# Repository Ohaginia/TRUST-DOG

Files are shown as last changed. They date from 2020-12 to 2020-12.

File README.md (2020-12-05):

# TRUST-DOG PROJECT
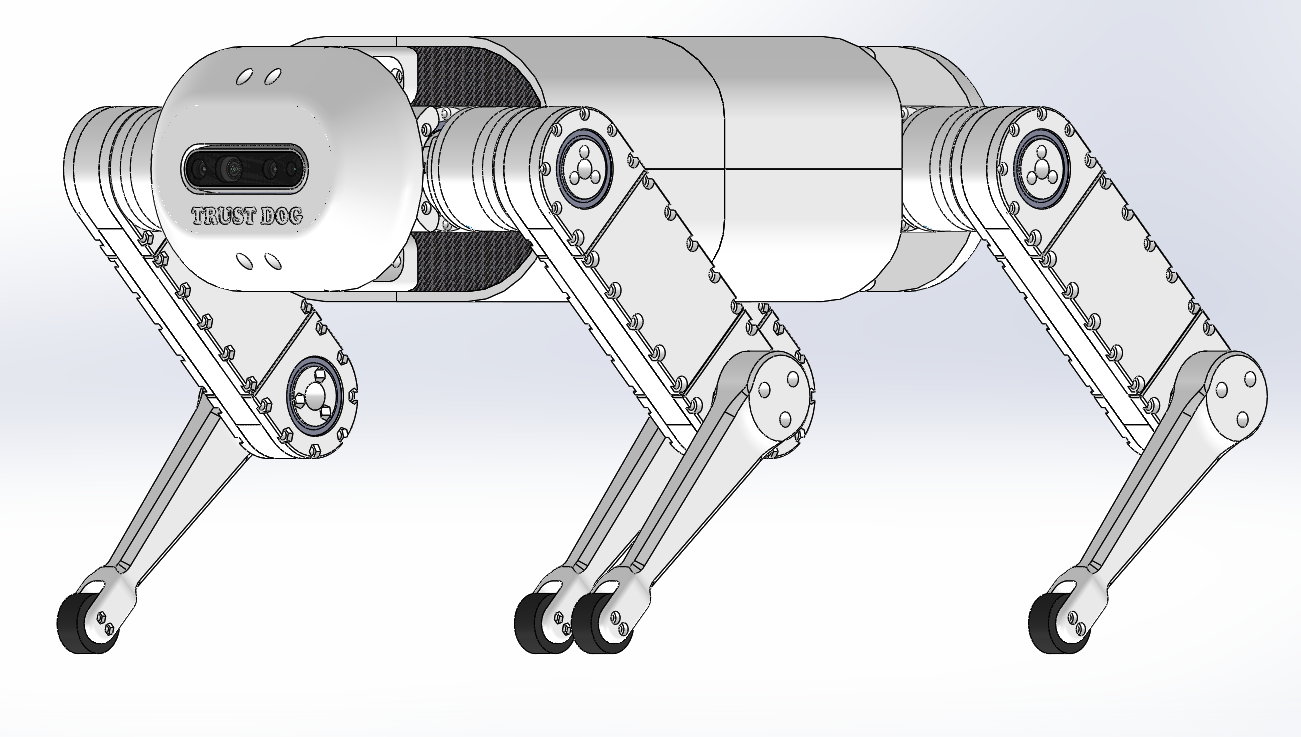
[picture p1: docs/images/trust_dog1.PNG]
trust_dog
      
 
## 0.プロジェクト概要
ドローン用ブラシレスモータを使って、Spot miniのような動的な制御ができる四足歩行ロボットを作るというプロジェクト。 
## 1.ハードウェア
### 1.1. ハードウェア概要

一脚につき3軸のアクチュエータを有する、全12軸四脚ロボット。  
構成自体はSpot miniやLaikagoと同じ。  
縦464[mm] × 横337[mm] × 高さ334[mm] (上図姿勢時）

### 1.2. アクチュエータ
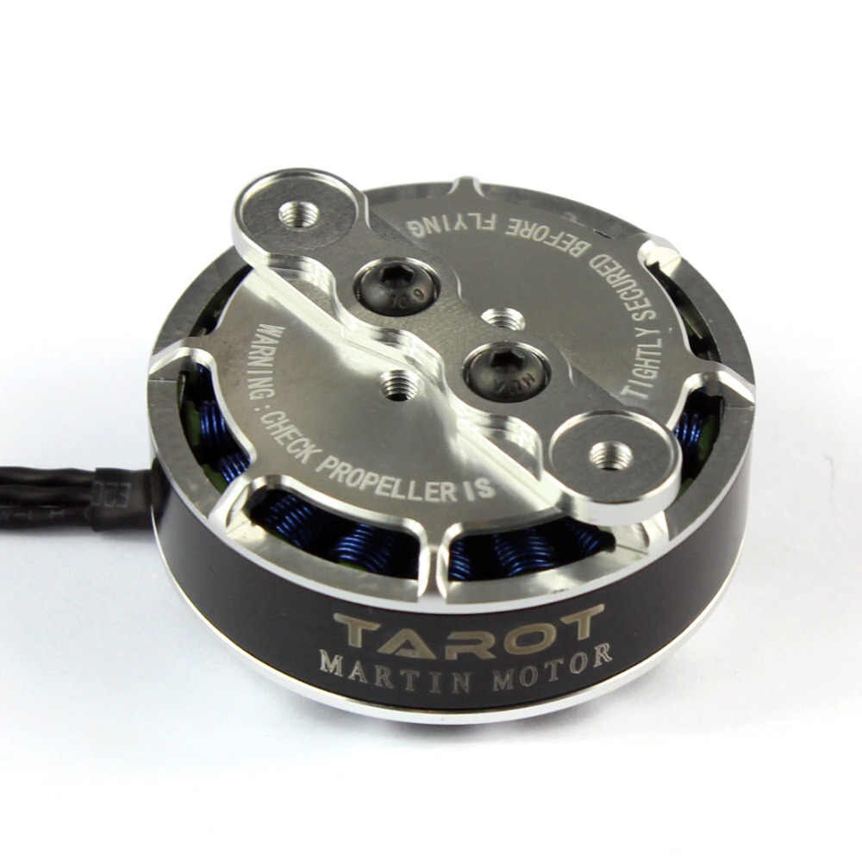
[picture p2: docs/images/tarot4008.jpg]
tarot4008
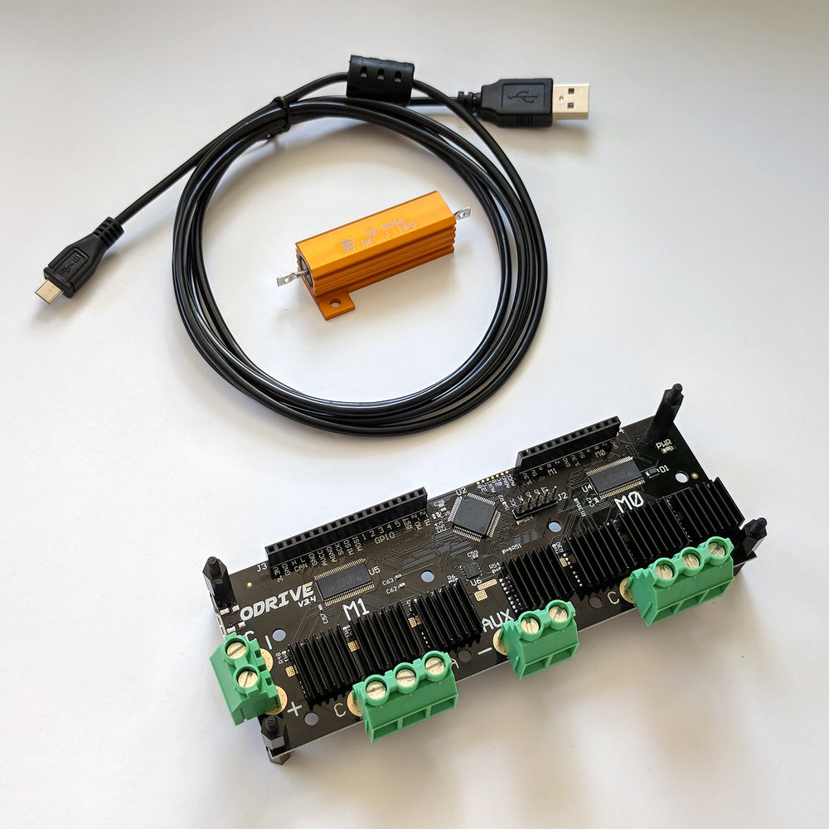
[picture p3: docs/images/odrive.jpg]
ODrive
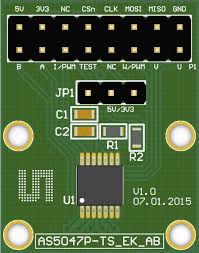
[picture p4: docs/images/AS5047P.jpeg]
AS5047P
  　    

+ モータ：[tarot4008　330kv](https://www.aliexpress.com/i/32697306634.html)
+ ドライバ：[Odrive v3.6](https://odriverobotics.com/)  
+ エンコーダ：[AS5047P](https://www.mouser.jp/ProductDetail/ams/AS5047P-TS_EK_AB?qs=Rt6VE0PE%2FOfJKFTMKo%252BL0Q%3D%3D)  

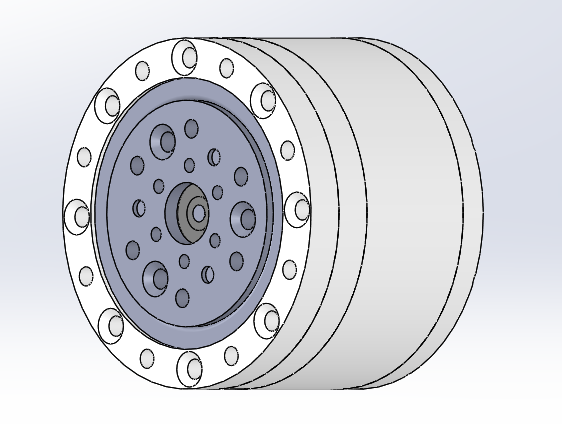
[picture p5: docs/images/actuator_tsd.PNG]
actuator1
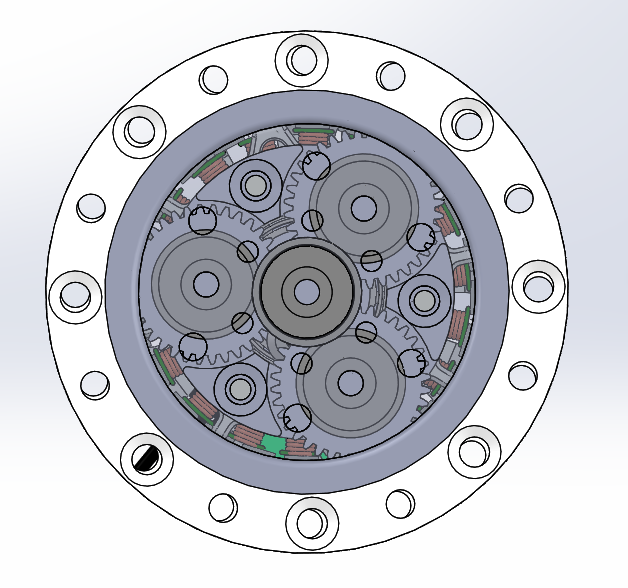
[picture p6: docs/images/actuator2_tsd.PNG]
     
TRUST DOGに使うアクチュエータには自作の遊星歯車減速機を使用しております。  
減速比は8/1でモータと一体型になっております。  
また、ギア部とシャフト部のみ金属加工品で他は３Dプリント品とコスト面や柔軟性も意識した設計となっております。

### 1.3. 脚
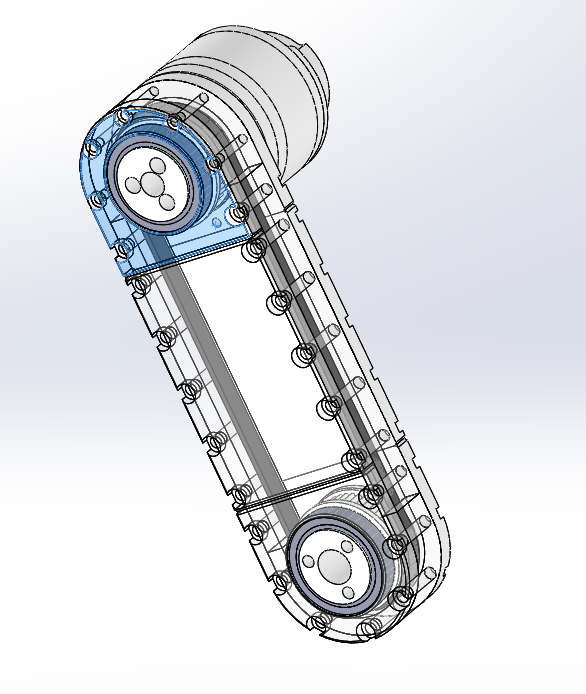
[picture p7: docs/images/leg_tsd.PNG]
    
脚は第1軸、第2軸はアクチュエータと直接接続されており、第3軸はベルト伝達機構となっております。  
ベルト伝達機構のメリットはバックラッシを軽減できるなどがあります。  
また、現時点でのベルト伝達機構の減速比は１：１ですが、トルクが必要となったとき簡単に設計が変更できる柔軟性も大きなメリットです。  
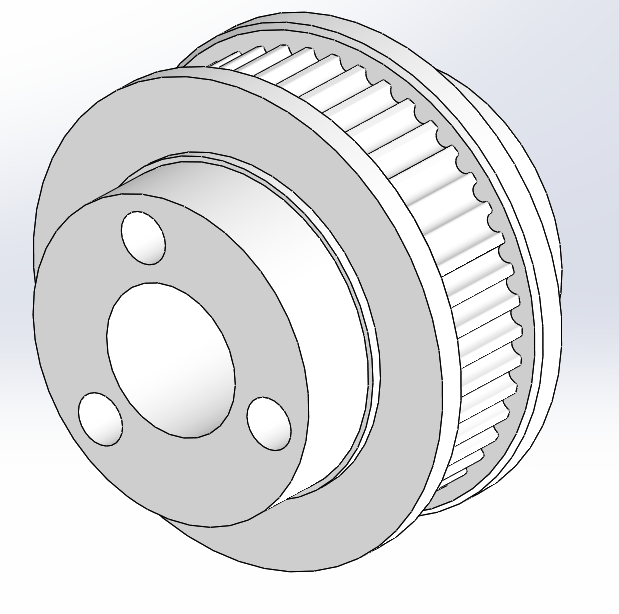
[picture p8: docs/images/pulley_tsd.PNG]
pulley
  
プーリーは３Dプリント品なので非常に低コストです。

### 1.4 テストスタンド
逆運動学やインピーダンス制御の実験を行うスタンドです。  
まずはシンプルに2自由度の脚を使ってテストします。  
脚の接地部分にはフォースゲージがついており、脚の接地反力を測定します。  
また、脚の付け根部にはIMUと距離センサが搭載されており、随時これらのパラメータをモニタリングします。

## 2. ソフトウェア
### 2.1　使用環境
+ ROS: Melodic
+ 使用言語: C/C++

### 2.2 開発工程
1. 逆運動学による位置制御の実装　（現在：2020/12/04）
2. インピーダンス制御を用いた力制御の実装
3. 歩行アルゴリズムの実装

#### 2.2.1 逆運動学とは
[逆運動学](https://en.wikipedia.org/wiki/Inverse_kinematics)とは足先の位置座標から関節角度を計算する手法。

#### 2.2.2 インピーダンス制御とは
インピーダンス制御とは、脚先を仮想的なマス・バネ・ダンパ系と固定することで動物のような脚の柔軟性を実現できるという制御手法。
[この動画](https://youtu.be/9AXlkIq_FQM)のように脚の仮想インピーダンスを適切に調節することでジャンプすることも可能に！

インピーダンス制御と逆運動学を組み合わせることで、安定した歩行が可能になるという仮説をもとに開発を勧めていきます。

## 作成者

* 作成者：上原昇馬
* 所属：TRUST SMITH 株式会社/ 沖縄工業高等専門学校
* E-mail：Hamashoma@gmail.com

## ライセンス

"TRUST DOG" プロジェクトは [MIT license](https://en.wikipedia.org/wiki/MIT_License)である。

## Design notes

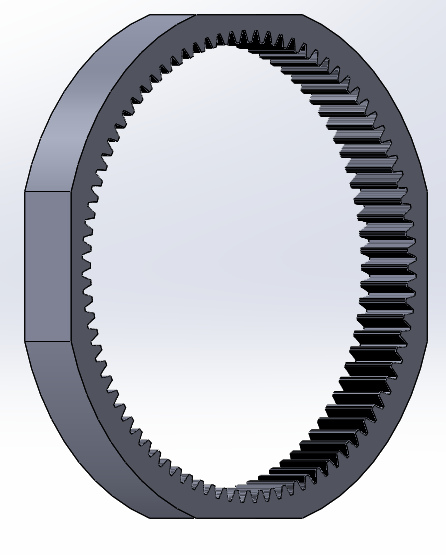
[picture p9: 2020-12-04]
tsd_hardware/Actuator/picture/ring-small_st.PNG

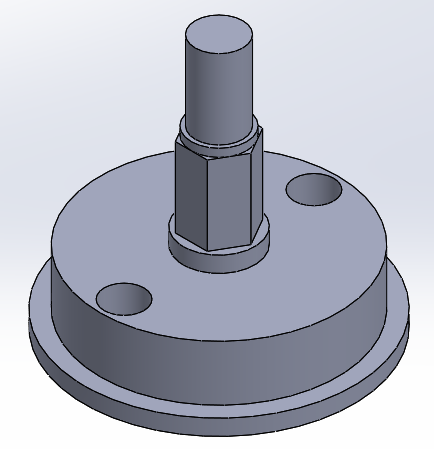
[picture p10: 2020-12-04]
tsd_hardware/Actuator/picture/Ishaft-small_al.PNG

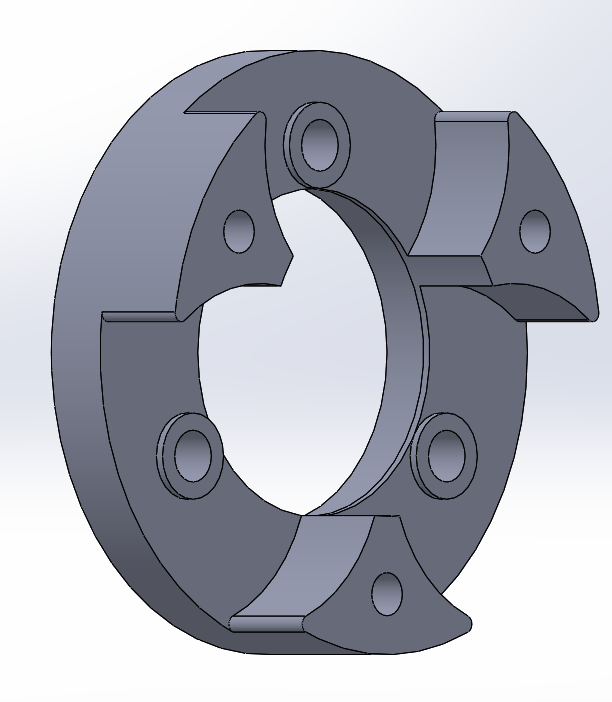
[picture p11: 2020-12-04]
tsd_hardware/Actuator/picture/planet-holder-small_al.PNG

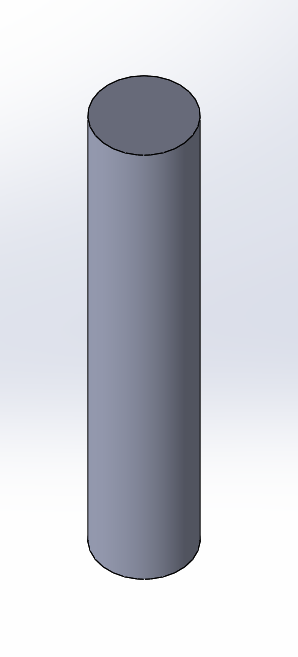
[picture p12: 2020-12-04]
tsd_hardware/Actuator/picture/planet-shaft-small.PNG

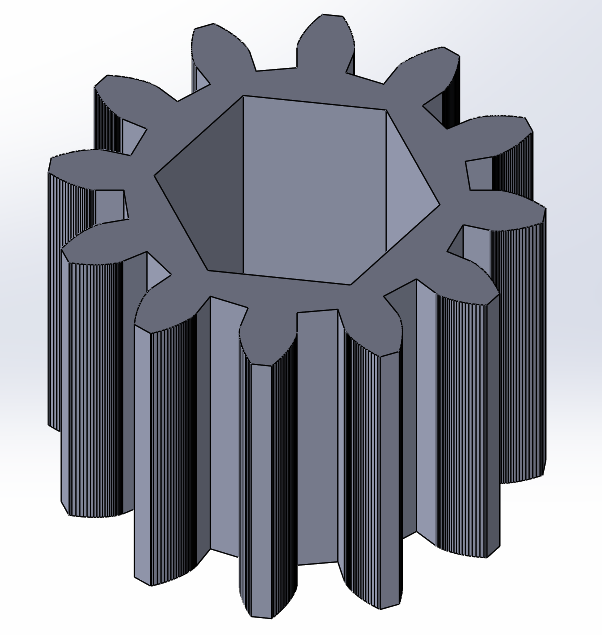
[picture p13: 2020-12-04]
tsd_hardware/Actuator/picture/sun-small_st.PNG

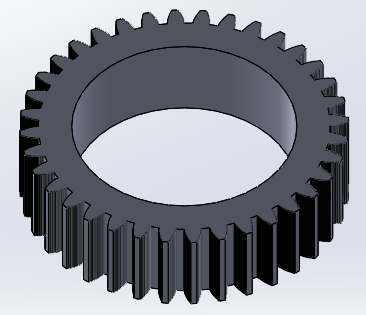
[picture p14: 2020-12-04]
tsd_hardware/Actuator/picture/planet-small_st.PNG

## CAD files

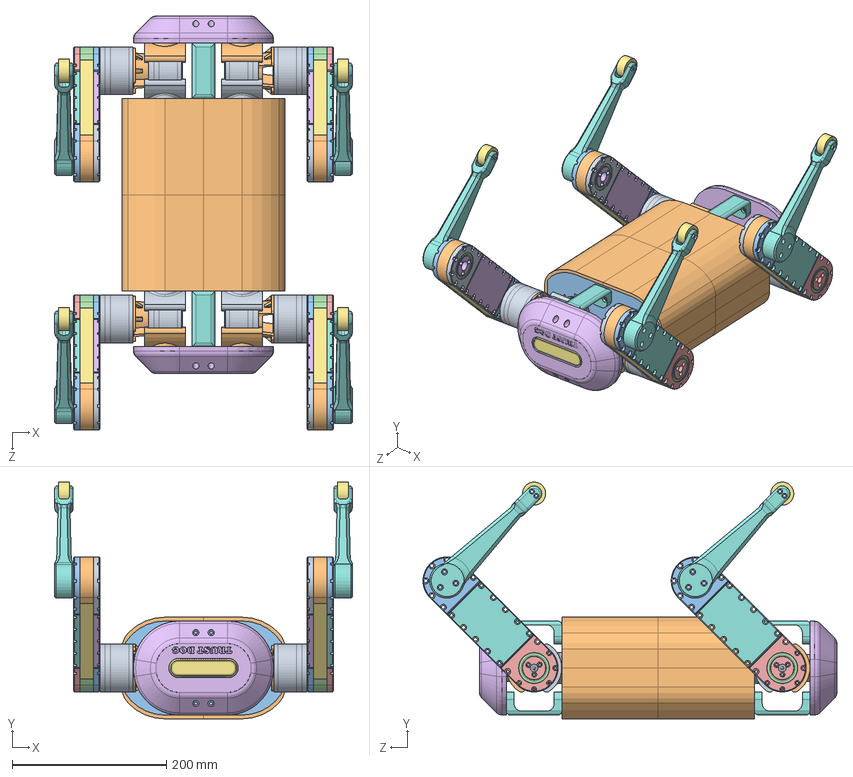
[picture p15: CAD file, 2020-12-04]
tsd_hardware/Asem/trustdog_tsd.SLDASM
387.0 x 307.2 x 537.1 mm
actuator1_tsd x 12
sholder3_tsd x 4
upper1_tsd x 4
upper2_tsd x 4
upper3_tsd x 4
upper4_tsd x 4
upper5_tsd x 8
upper6_tsd x 4
upper7_tsd x 4
upper8_tsd x 4
upper9_tsd x 4
B6806ZZ_tsd x 20
3GT-a_tsd x 4
3GT-b_tsd x 4
foot1_tsd x 4
lower1_tsd x 4
sholder1_tsd x 4
sholder2_tsd x 4
body1_tsd x 2
NFSL6-3030-100_tsd x 4
HFS5-2040-240_tsd x 2
body2_tsd x 2
IntelRealsense_D435_Multibody_tsd x 2
body3_tsd x 4
NFSL6-3030-180_tsd x 4
body4_tsd x 8

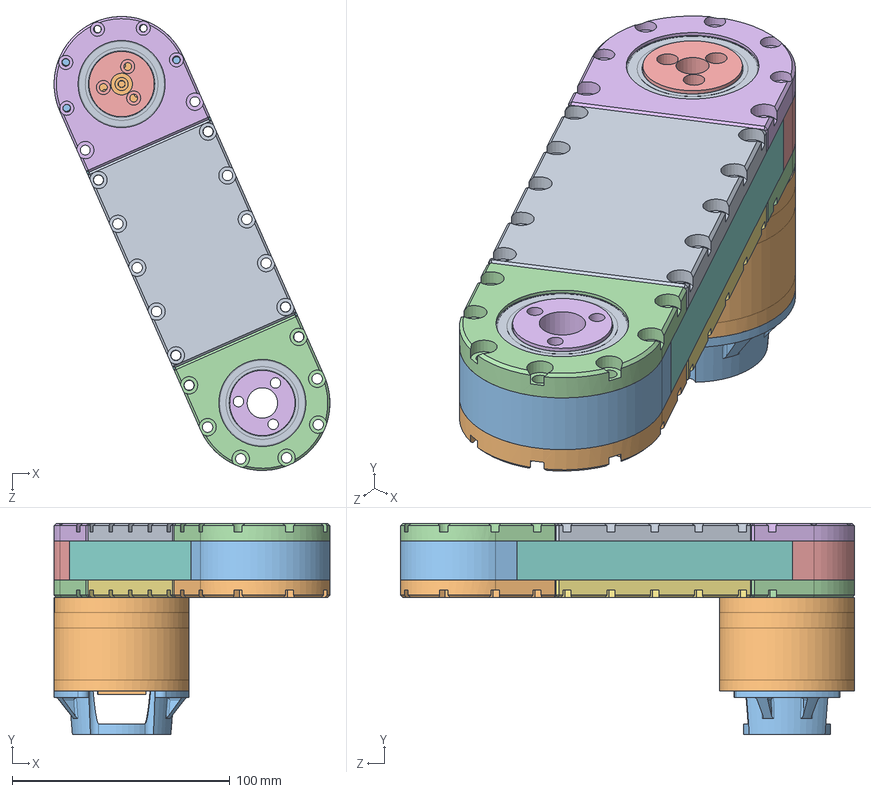
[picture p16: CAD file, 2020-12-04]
tsd_hardware/SubAsem/leg3.SLDASM
126.6 x 97.0 x 208.4 mm
actuator1_tsd
sholder3_tsd
upper1_tsd
upper2_tsd
upper3_tsd
upper4_tsd
upper5_tsd x 2
upper6_tsd
upper7_tsd
upper8_tsd
upper9_tsd
B6806ZZ_tsd x 4
3GT-a_tsd
3GT-b_tsd

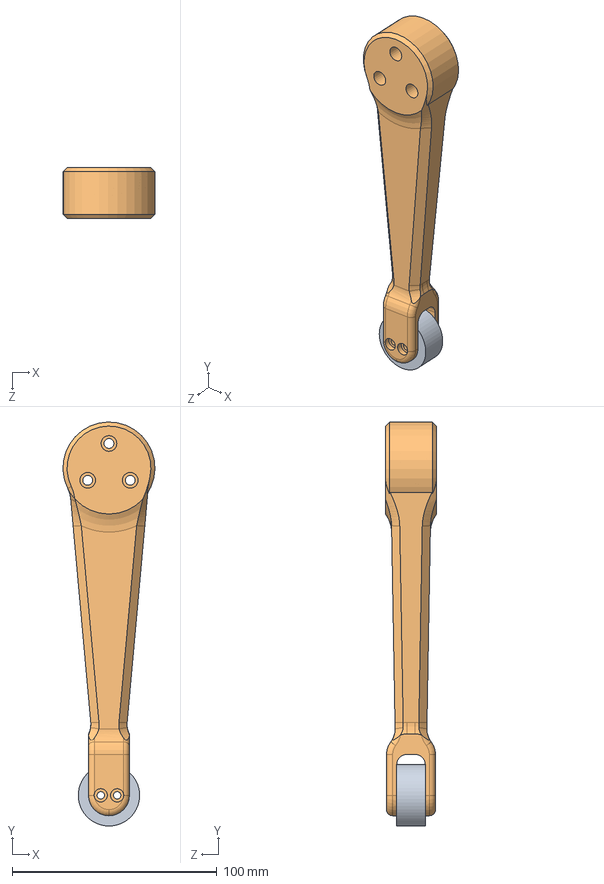
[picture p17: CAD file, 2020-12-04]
tsd_hardware/SubAsem/leg4.SLDASM
44.9 x 197.5 x 25.0 mm
foot1_tsd
lower1_tsd

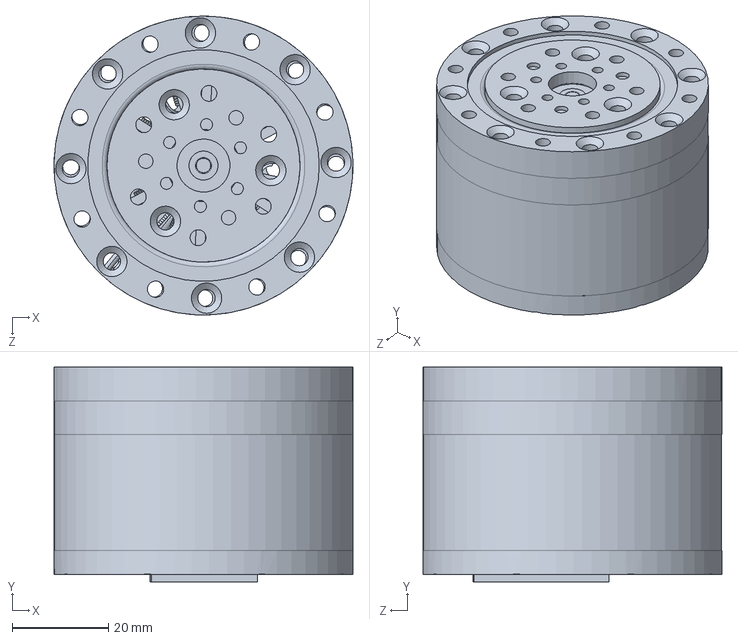
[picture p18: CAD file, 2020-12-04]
tsd_hardware/SubAsem/leg1.SLDASM
62.0 x 44.5 x 62.0 mm

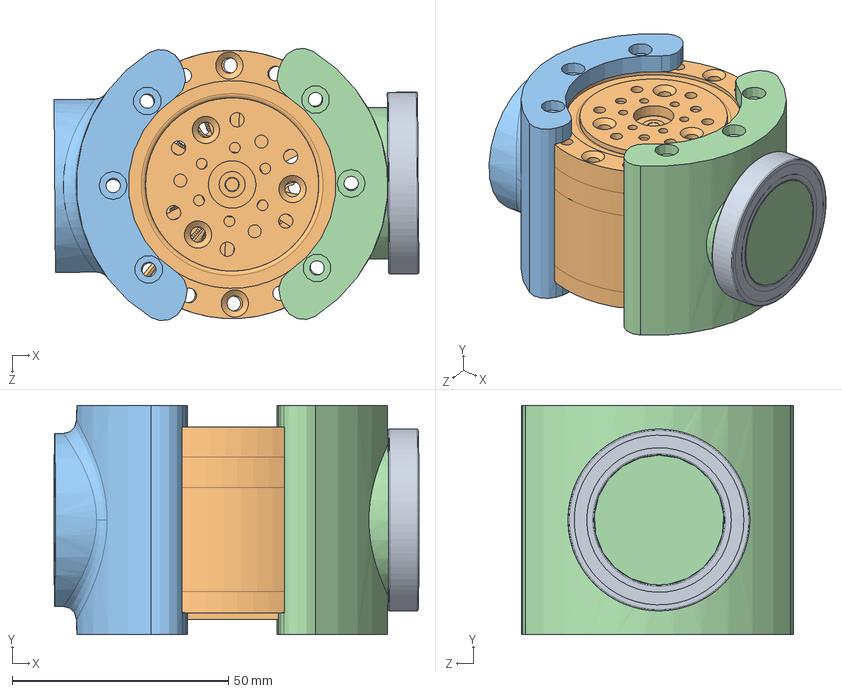
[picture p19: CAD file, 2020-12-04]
tsd_hardware/SubAsem/leg2.SLDASM
84.3 x 53.0 x 62.9 mm
actuator1_tsd
sholder1_tsd
sholder2_tsd
B6806ZZ_tsd

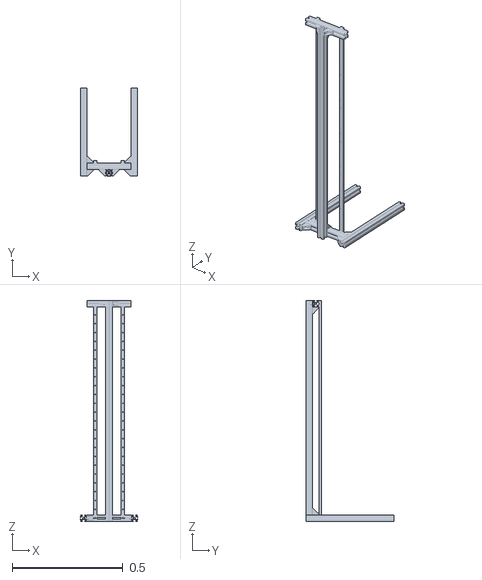
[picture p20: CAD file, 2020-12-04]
test/tsdt_description/meshes/stand.STL
0.26 x 0.4 x 1

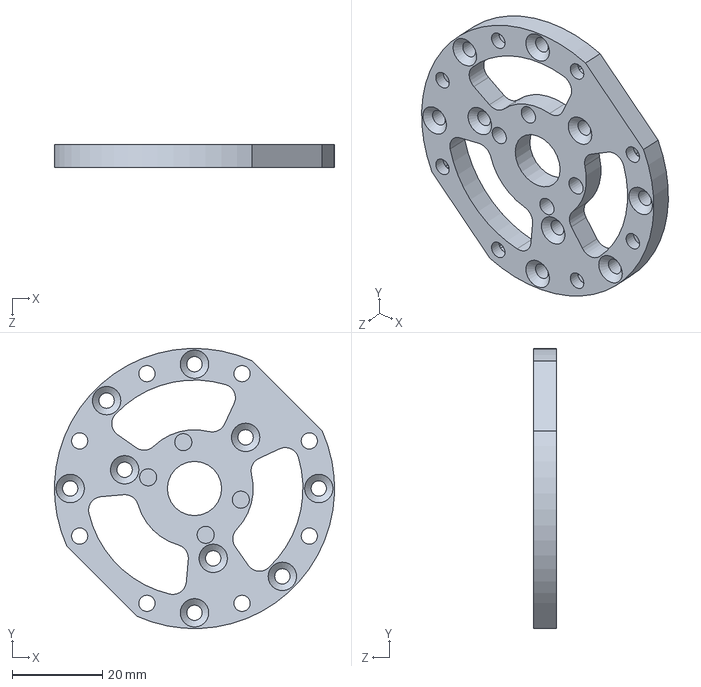
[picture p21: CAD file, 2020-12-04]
tsd_hardware/Actuator/3dPrint/plate-small_3D.SLDPRT
62.0 x 62.0 x 5.00 mm

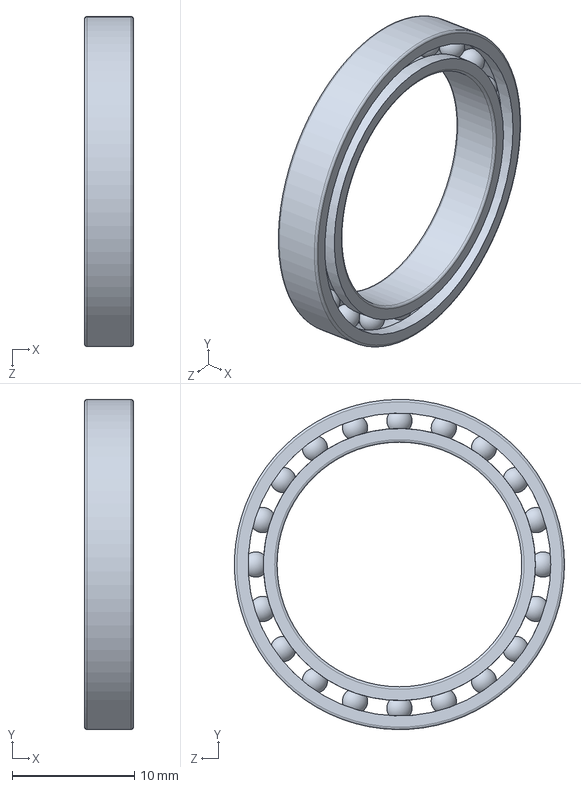
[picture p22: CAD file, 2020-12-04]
tsd_hardware/Actuator/bearing/6704.SLDPRT
4.00 x 27.0 x 27.0 mm

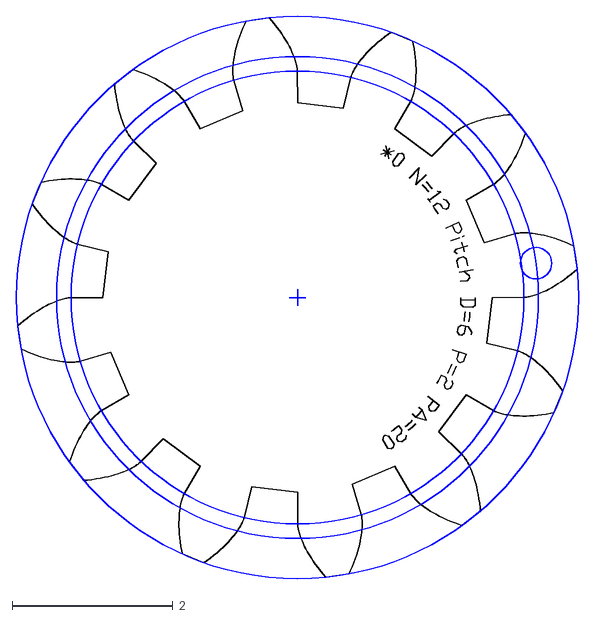
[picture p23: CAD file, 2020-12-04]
tsd_hardware/Actuator/GearDXF/sun-gear.dxf
7.00 x 7.00

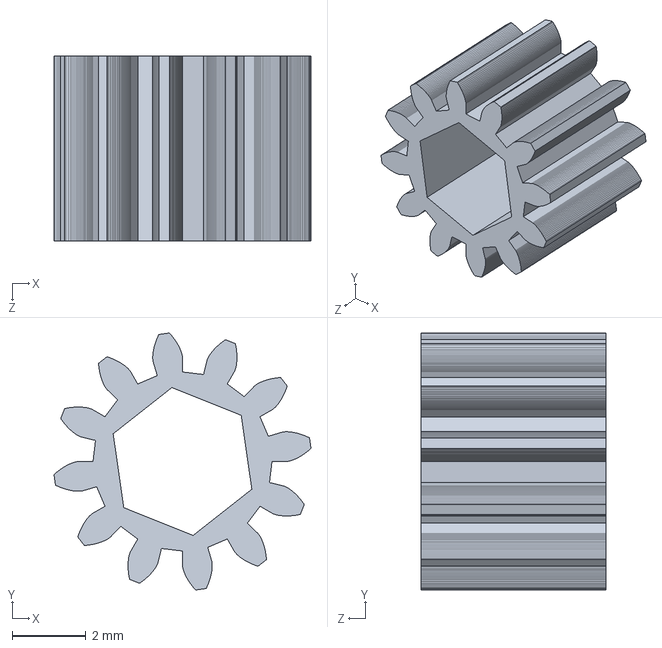
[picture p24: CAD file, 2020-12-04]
tsd_hardware/Actuator/Metal manufacturing/sun-small_st.SLDPRT
6.96 x 6.96 x 5.00 mm

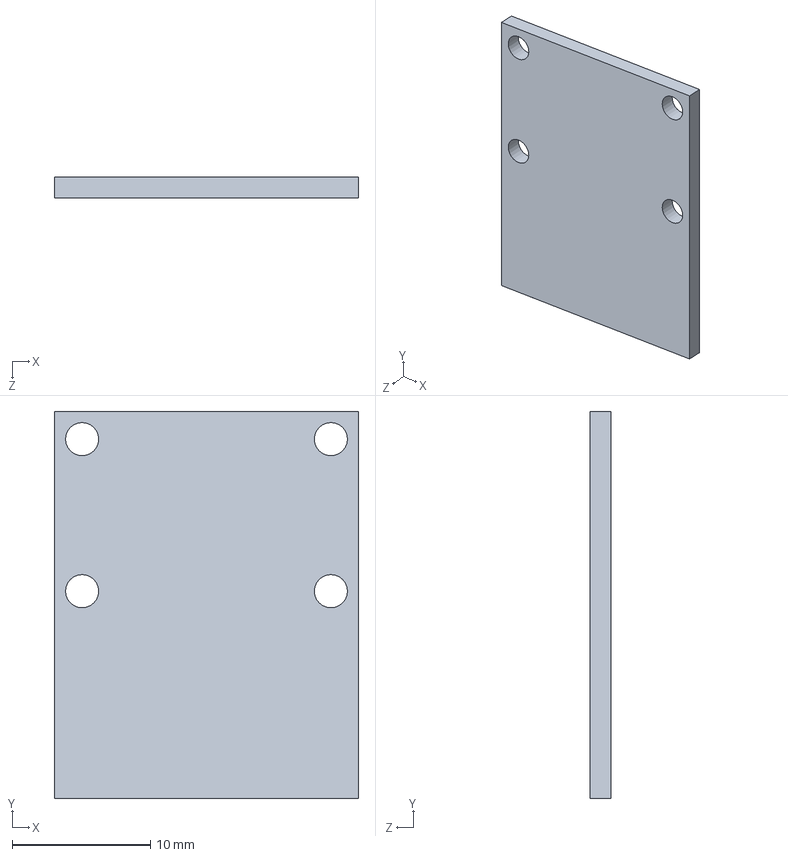
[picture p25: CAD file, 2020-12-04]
tsd_hardware/Actuator/motor/encoder.SLDPRT
22.0 x 28.0 x 1.50 mm

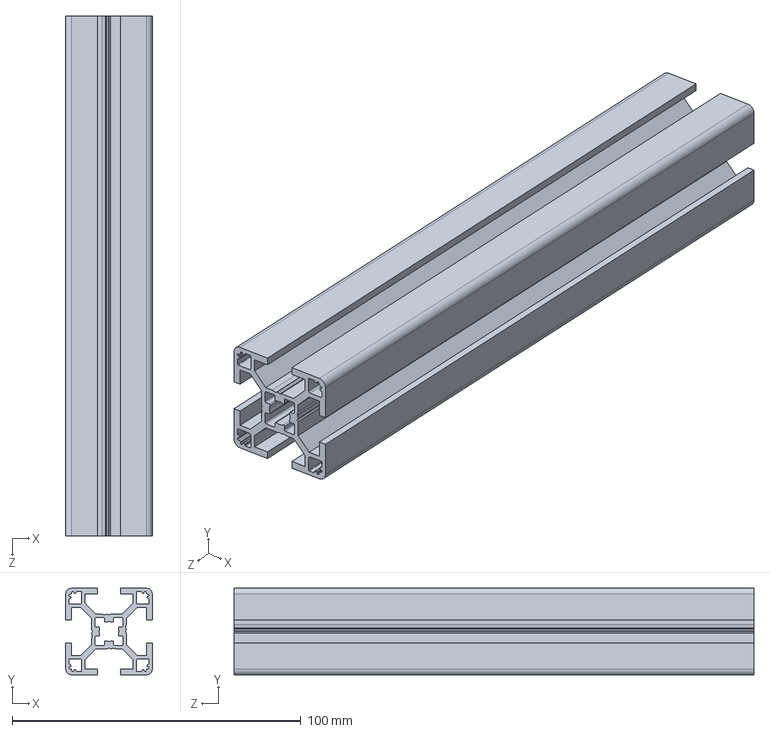
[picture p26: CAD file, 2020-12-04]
tsd_hardware/OTS/alumium frame/NFSL6-3030-180_tsd.SLDPRT
30.0 x 30.0 x 180.0 mm

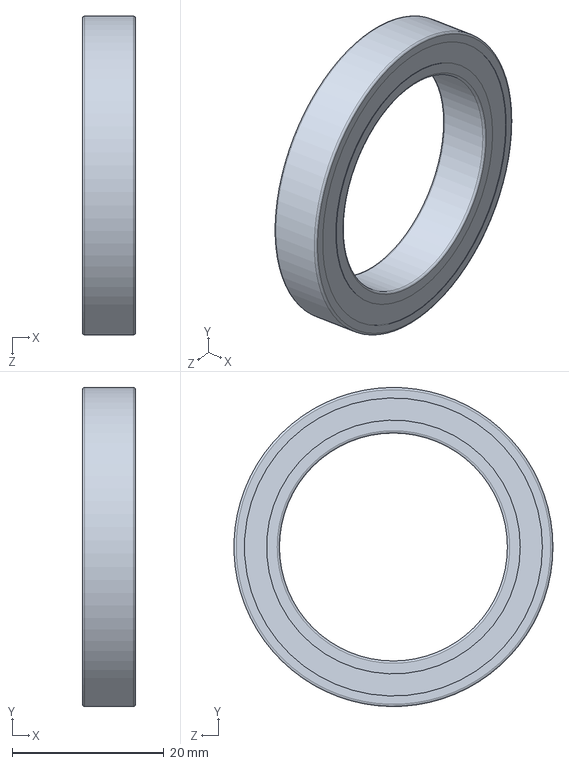
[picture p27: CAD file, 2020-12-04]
tsd_hardware/OTS/bearing/B6806ZZ_tsd.SLDPRT
7.00 x 42.0 x 42.0 mm

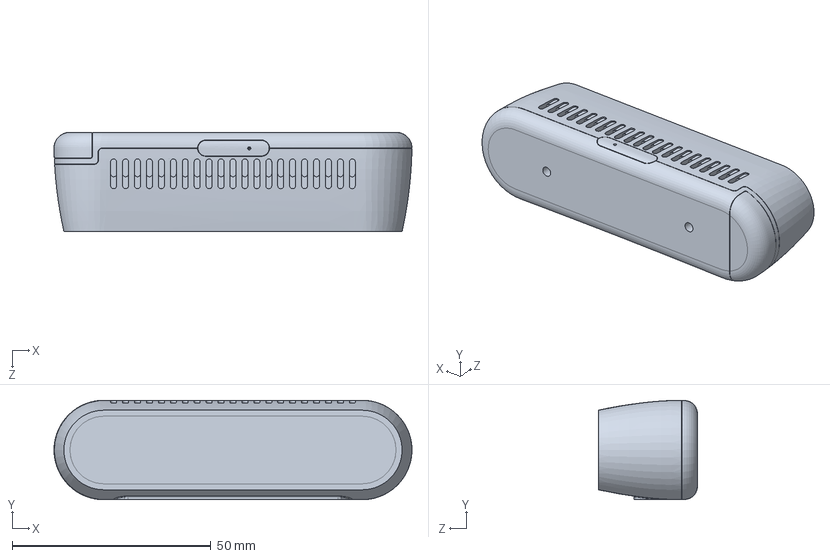
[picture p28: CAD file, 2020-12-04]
tsd_hardware/OTS/camera/IntelRealsense_D435_Multibody_tsd.SLDPRT
90.0 x 25.0 x 25.0 mm

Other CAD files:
tsd_hardware/Actuator/Assembly/actuator1_tsd.SLDPRT
tsd_hardware/Part/lower1_tsd.SLDPRT
test/tsdt_description/meshes/leg1.STL
tsd_hardware/Actuator/3dPrint/housing-small_3D.SLDPRT
test/tsdt_description/meshes/leg2.STL
test/tsdt_description/meshes/leg3.STL
tsd_hardware/Actuator/3dPrint/Eholder-small_3D.SLDPRT
tsd_hardware/Actuator/3dPrint/cap-small_3D.SLDPRT
tsd_hardware/Actuator/3dPrint/cap-small_3D.STL
tsd_hardware/Actuator/3dPrint/plate2-small_3D.SLDPRT
tsd_hardware/Actuator/3dPrint/ring-holder-small_3D.SLDPRT
tsd_hardware/Actuator/3dPrint/ring-holder-small_3D.STL
tsd_hardware/Actuator/GearDXF/internal-gear.dxf
tsd_hardware/Actuator/GearDXF/planet-gear.dxf
tsd_hardware/Actuator/Metal manufacturing/Ishaft-small2_al.SLDPRT
tsd_hardware/Actuator/Metal manufacturing/magnet-screw.SLDPRT
tsd_hardware/Actuator/Metal manufacturing/output-plate-small2_al.SLDPRT
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

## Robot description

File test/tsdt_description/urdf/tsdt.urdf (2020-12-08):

<?xml version="1.0" encoding="utf-8"?>
<!-- =================================================================================== -->
<!-- |    This document was autogenerated by xacro from tsdt.urdf.xacro                | -->
<!-- |    EDITING THIS FILE BY HAND IS NOT RECOMMENDED                                 | -->
<!-- =================================================================================== -->
<robot name="tsdt">
  <material name="white">
    <color rgba="1.0 1.0 1.0 1.0"/>
  </material>
  <link name="world"/>
  <joint name="fixed" type="fixed">
    <parent link="world"/>
    <child link="stand"/>
  </joint>
  <link name="stand">
    <visual>
      <geometry>
        <mesh filename="package://tsdt_description/meshes/stand.STL"/>
      </geometry>
      <origin rpy="0 0 0" xyz="0 0 0"/>
      <material name="white"/>
    </visual>
    <collision>
      <geometry>
        <mesh filename="package://tsdt_description/meshes/stand.STL"/>
      </geometry>
      <origin rpy="0 0 0" xyz="0 0 0"/>
    </collision>
    <inertial>
      <mass value="5.0"/>
      <origin rpy="0 0 0" xyz="0 0 0 "/>
      <inertia ixx="0" ixy="0" ixz="0" iyy="0" iyz="0" izz="0"/>
    </inertial>
  </link>
  <!--joint name="joint0" type="fixed">
    <origin xyz="0 0 0.82" rpy="0 0 0"/>
    <parent link="stand"/>
    <child link="leg1"/>
  </joint-->
  <joint name="joint0" type="prismatic">
    <origin rpy="0 0 0" xyz="0 0 0.82"/>
    <axis xyz="0 0 1"/>
    <parent link="stand"/>
    <child link="leg1"/>
    <limit effort="100" lower="-0.738" upper="0.098" velocity="1.0"/>
  </joint>
  <link name="leg1">
    <visual>
      <geometry>
        <mesh filename="package://tsdt_description/meshes/leg1.STL"/>
      </geometry>
      <origin rpy="0 0 0" xyz="0 0 -0.82"/>
      <material name="white"/>
    </visual>
    <collision>
      <geometry>
        <mesh filename="package://tsdt_description/meshes/leg1.STL"/>
      </geometry>
      <origin rpy="0 0 0" xyz="0 0 -0.82"/>
    </collision>
    <inertial>
      <mass value="5.0"/>
      <origin rpy="0 0 0" xyz="0 0 0 "/>
      <inertia ixx="0" ixy="0" ixz="0" iyy="0" iyz="0" izz="0"/>
    </inertial>
  </link>
  <joint name="joint1" type="continuous">
    <origin rpy="0 0 0" xyz="0 0.043 0"/>
    <axis xyz="0 1 0"/>
    <parent link="leg1"/>
    <child link="leg2"/>
  </joint>
  <link name="leg2">
    <visual>
      <geometry>
        <mesh filename="package://tsdt_description/meshes/leg2.STL"/>
      </geometry>
      <origin rpy="0 0 0" xyz="0 -0.043 -0.82"/>
      <material name="white"/>
    </visual>
    <collision>
      <geometry>
        <mesh filename="package://tsdt_description/meshes/leg2.STL"/>
      </geometry>
      <origin rpy="0 0 0" xyz="0 -0.043 -0.82"/>
    </collision>
    <inertial>
      <mass value="5.0"/>
      <origin rpy="0 0 0" xyz="0 0 0 "/>
      <inertia ixx="0" ixy="0" ixz="0" iyy="0" iyz="0" izz="0"/>
    </inertial>
  </link>
  <joint name="joint2" type="continuous">
    <origin rpy="0 0 0" xyz="0 0.097 -0.16"/>
    <axis xyz="0 1 0"/>
    <parent link="leg2"/>
    <child link="leg3"/>
  </joint>
  <link name="leg3">
    <visual>
      <geometry>
        <mesh filename="package://tsdt_description/meshes/leg3.STL"/>
      </geometry>
      <origin rpy="0 0 0" xyz="0 -0.14 -0.66"/>
      <material name="white"/>
    </visual>
    <collision>
      <geometry>
        <mesh filename="package://tsdt_description/meshes/leg2.STL"/>
      </geometry>
      <origin rpy="0 0 0" xyz="0 -0.14 -0.66"/>
    </collision>
    <inertial>
      <mass value="5.0"/>
      <origin rpy="0 0 0" xyz="0 0 0 "/>
      <inertia ixx="0" ixy="0" ixz="0" iyy="0" iyz="0" izz="0"/>
    </inertial>
  </link>
  <joint name="joint3" type="fixed">
    <origin rpy="0 0 0" xyz="0 0 -0.16"/>
    <parent link="leg3"/>
    <child link="leg4"/>
  </joint>
  <link name="leg4"/>
</robot>

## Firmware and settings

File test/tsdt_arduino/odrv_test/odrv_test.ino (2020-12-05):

/***+++++++++++++++++odrive_tool************************/
#include <ODriveTool.h>
// Printing with stream operator helper functions
template<class T> inline Print& operator <<(Print &obj,     T arg) { obj.print(arg);    return obj; }
template<>        inline Print& operator <<(Print &obj, float arg) { obj.print(arg, 4); return obj; }
/*******************************************************/
#define LED_BUILTIN 15 //debug led
const int num_motor=2; //motor quantity
const float pi=3.14159262;

ODriveTool odrive(Serial2); //odrive object


/********************network_config*********************/
#include <WiFi.h>
#include <ESPmDNS.h>
#include <WiFiUdp.h>
#include <ArduinoOTA.h>
const char* ssid = "*****";
const char* password = "*****";
/********************************************************/  

// the setup function runs once when you press reset or power the board
void setup() {  
  /********************network_config*********************/
  Serial.begin(115200);
  Serial.println("Booting");
  WiFi.mode(WIFI_STA);
  WiFi.begin(ssid, password);
  while (WiFi.waitForConnectResult() != WL_CONNECTED) {
    Serial.println("Connection Failed! Rebooting...");
    delay(5000);
    ESP.restart();
  }
  ArduinoOTA
    .onStart([]() {
      String type;
      if (ArduinoOTA.getCommand() == U_FLASH)
        type = "sketch";
      else // U_SPIFFS
        type = "filesystem";

      // NOTE: if updating SPIFFS this would be the place to unmount SPIFFS using SPIFFS.end()
      Serial.println("Start updating " + type);
    })
    .onEnd([]() {
      Serial.println("\nEnd");
    })
    .onProgress([](unsigned int progress, unsigned int total) {
      Serial.printf("Progress: %u%%\r", (progress / (total / 100)));
    })
    .onError([](ota_error_t error) {
      Serial.printf("Error[%u]: ", error);
      if (error == OTA_AUTH_ERROR) Serial.println("Auth Failed");
      else if (error == OTA_BEGIN_ERROR) Serial.println("Begin Failed");
      else if (error == OTA_CONNECT_ERROR) Serial.println("Connect Failed");
      else if (error == OTA_RECEIVE_ERROR) Serial.println("Receive Failed");
      else if (error == OTA_END_ERROR) Serial.println("End Failed");
    });

  ArduinoOTA.begin();

  Serial.println("Ready");
  Serial.print("IP address: ");
  Serial.println(WiFi.localIP());
  /********************************************************/  
  
  pinMode(LED_BUILTIN, OUTPUT); //pin number defined
  odrive.odrive_reboot(); // reboot
  for(int motor=0; motor< num_motor; motor++){
     odrive.odrive_init(motor,true,20.0); //
  }
}


void loop() {
  ArduinoOTA.handle(); //network_config
  
  digitalWrite(LED_BUILTIN, HIGH);   // turn the LED on (HIGH is the voltage level)
  delay(100);                       // wait for a second
  digitalWrite(LED_BUILTIN, LOW);    // turn the LED off by making the voltage LOW
  delay(100);  

   for (float ph = 0.0f; ph < 6.28318530718f; ph += 0.01f) {
        float pos_m0 = 4.0f * cos(ph);
        odrive.SetPosition(0, pos_m0);
        delay(5);
      }
    }

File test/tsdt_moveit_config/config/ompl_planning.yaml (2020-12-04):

planner_configs:
  SBL:
    type: geometric::SBL
    range: 0.0  # Max motion added to tree. ==> maxDistance_ default: 0.0, if 0.0, set on setup()
  EST:
    type: geometric::EST
    range: 0.0  # Max motion added to tree. ==> maxDistance_ default: 0.0, if 0.0 setup()
    goal_bias: 0.05  # When close to goal select goal, with this probability. default: 0.05
  LBKPIECE:
    type: geometric::LBKPIECE
    range: 0.0  # Max motion added to tree. ==> maxDistance_ default: 0.0, if 0.0, set on setup()
    border_fraction: 0.9  # Fraction of time focused on boarder default: 0.9
    min_valid_path_fraction: 0.5  # Accept partially valid moves above fraction. default: 0.5
  BKPIECE:
    type: geometric::BKPIECE
    range: 0.0  # Max motion added to tree. ==> maxDistance_ default: 0.0, if 0.0, set on setup()
    border_fraction: 0.9  # Fraction of time focused on boarder default: 0.9
    failed_expansion_score_factor: 0.5  # When extending motion fails, scale score by factor. default: 0.5
    min_valid_path_fraction: 0.5  # Accept partially valid moves above fraction. default: 0.5
  KPIECE:
    type: geometric::KPIECE
    range: 0.0  # Max motion added to tree. ==> maxDistance_ default: 0.0, if 0.0, set on setup()
    goal_bias: 0.05  # When close to goal select goal, with this probability. default: 0.05
    border_fraction: 0.9  # Fraction of time focused on boarder default: 0.9 (0.0,1.]
    failed_expansion_score_factor: 0.5  # When extending motion fails, scale score by factor. default: 0.5
    min_valid_path_fraction: 0.5  # Accept partially valid moves above fraction. default: 0.5
  RRT:
    type: geometric::RRT
    range: 0.0  # Max motion added to tree. ==> maxDistance_ default: 0.0, if 0.0, set on setup()
    goal_bias: 0.05  # When close to goal select goal, with this probability? default: 0.05
  RRTConnect:
    type: geometric::RRTConnect
    range: 0.0  # Max motion added to tree. ==> maxDistance_ default: 0.0, if 0.0, set on setup()
  RRTstar:
    type: geometric::RRTstar
    range: 0.0  # Max motion added to tree. ==> maxDistance_ default: 0.0, if 0.0, set on setup()
    goal_bias: 0.05  # When close to goal select goal, with this probability? default: 0.05
    delay_collision_checking: 1  # Stop collision checking as soon as C-free parent found. default 1
  TRRT:
    type: geometric::TRRT
    range: 0.0  # Max motion added to tree. ==> maxDistance_ default: 0.0, if 0.0, set on setup()
    goal_bias: 0.05  # When close to goal select goal, with this probability? default: 0.05
    max_states_failed: 10  # when to start increasing temp. default: 10
    temp_change_factor: 2.0  # how much to increase or decrease temp. default: 2.0
    min_temperature: 10e-10  # lower limit of temp change. default: 10e-10
    init_temperature: 10e-6  # initial temperature. default: 10e-6
    frountier_threshold: 0.0  # dist new state to nearest neighbor to disqualify as frontier. default: 0.0 set in setup()
    frountierNodeRatio: 0.1  # 1/10, or 1 nonfrontier for every 10 frontier. default: 0.1
    k_constant: 0.0  # value used to normalize expresssion. default: 0.0 set in setup()
  PRM:
    type: geometric::PRM
    max_nearest_neighbors: 10  # use k nearest neighbors. default: 10
  PRMstar:
    type: geometric::PRMstar
  FMT:
    type: geometric::FMT
    num_samples: 1000  # number of states that the planner should sample. default: 1000
    radius_multiplier: 1.1  # multiplier used for the nearest neighbors search radius. default: 1.1
    nearest_k: 1  # use Knearest strategy. default: 1
    cache_cc: 1  # use collision checking cache. default: 1
    heuristics: 0  # activate cost to go heuristics. default: 0
    extended_fmt: 1  # activate the extended FMT*: adding new samples if planner does not finish successfully. default: 1
  BFMT:
    type: geometric::BFMT
    num_samples: 1000  # number of states that the planner should sample. default: 1000
    radius_multiplier: 1.0  # multiplier used for the nearest neighbors search radius. default: 1.0
    nearest_k: 1  # use the Knearest strategy. default: 1
    balanced: 0  # exploration strategy: balanced true expands one tree every iteration. False will select the tree with lowest maximum cost to go. default: 1
    optimality: 1  # termination strategy: optimality true finishes when the best possible path is found. Otherwise, the algorithm will finish when the first feasible path is found. default: 1
    heuristics: 1  # activates cost to go heuristics. default: 1
    cache_cc: 1  # use the collision checking cache. default: 1
    extended_fmt: 1  # Activates the extended FMT*: adding new samples if planner does not finish successfully. default: 1
  PDST:
    type: geometric::PDST
  STRIDE:
    type: geometric::STRIDE
    range: 0.0  # Max motion added to tree. ==> maxDistance_ default: 0.0, if 0.0, set on setup()
    goal_bias: 0.05  # When close to goal select goal, with this probability. default: 0.05
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

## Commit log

2020-12-04 add cad file
    [3GT-a_tsd.SLDPRT, 3GT-b_tsd.SLDPRT, 6704.SLDPRT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]
2020-12-05 fix arduino program
2020-12-08 create visual node
    [tsdt.urdf]
